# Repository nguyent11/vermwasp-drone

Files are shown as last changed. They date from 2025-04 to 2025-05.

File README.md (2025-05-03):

# Wasp Drone
Senior Capstone Project for CSE 4316 and CSE 4317 Computer System Design Project I and II at UT Arlington Department of Computer Science and Engineering by team Verminator.

## Summary of Work
In this project, we propose a design for an aerial spraying platform. The idea is to have insecticide sprayers mounted onto a drone. Then, the product can be used to spray insecticides on wasp nests, or other insect nests, in hard to reach areas.

This repository contains source code, links to other repositories, STL files for 3D models, and other documentation used in the development of this project.

## Getting Started
This repository contains source code and links to other repositories with source code. After cloning this repository, run the following command to obtain source code from included submodules:
```
  git submodule update --init  --recursive
```

## About the Team
The team is named after Dwayne LaFontant aka The Verminator from Over the Hedge produced by DreamWorks. The team's emblem takes inspiration from Helldivers 2 by Arrowhead Game Studios.

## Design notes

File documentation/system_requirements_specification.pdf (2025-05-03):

## DEPARTMENT OF COMPUTER SCIENCE & ENGINEERING

## THE UNIVERSITY OF TEXAS AT ARLINGTON

## SYSTEM REQUIREMENTS SPECIFICATION

# CSE 4316: SENIOR DESIGN I FALL 2024

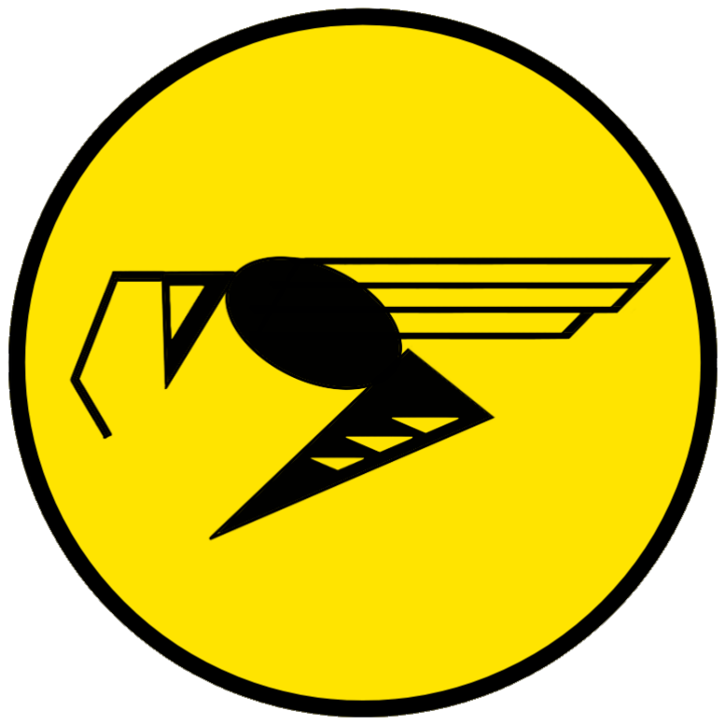
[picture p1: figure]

## VERMINATOR

## WASP DRONE

ISAAC MEDRANO
LUIS NAREZ
TYLER NGUYEN
NISHCHAL SHRESTHA
RAJESH YAKSHO
Verminator - Fall 2024 | page 1 of 28

REVISION HISTORY

Revision | Date | Author(s) | Description
0.1 | 10.01.2024 | TN | document creation
0.2 | 10.12.2024 | IM, LN, TN, NS, RY | complete draft
1.0 | 10.14.2024 | IM, LN, TN, NS, RY | oficial release
2.0 | 05.01.2025 | LN, TN, RY | Updated to reflect changing project requirements

CONTENTS

1 Product Concept | 8
2 Product Description | 9
3 Customer Requirements | 11

4 Packaging Requirements | 15
5 Performance Requirements | 17
6 Safety Requirements | 18

7 Security Requirements | 20
8 Maintenance & Support Requirements | 21
9 Other Requirements | 23
10 Future Items | 24

LIST OF FIGURES

1 | Product Concept of the Wasp Drone | | 9
2 | Wiring Overview (from Cube Orange+ Documentation) | | 21
3 | Power Systems Overview (from Cube Orange+ Documentation) | | 22

### 1 PRODUCT CONCEPT

This section describes the purpose, use and intended user audience for the Wasp Drone product. Wasp Drone is a system that remotely exterminates wasp nests and other pests. Users of Wasp Drone will be able to safely exterminate wasp nests, spray venom, and remotely operate with a controller and live feed camera.

### 1.1 PURPOSE AND USE

Wasp Drone will be sent in to neutralize wasp nests without the need for a human exterminator. The purpose of Wasp Drone is to provide a safe alternative for wasp extermination without putting exterminators in harm’s way. Its venom delivery system can be modified to spray other liquids so there is versatility in agricultural applications (delivering insecticides, herbicides, fertilizer, and water). Wasp Drone’s live feed feature can be used for filming and streaming applications as well.

### 1.2 INTENDED AUDIENCE

- Exterminators: The primary users for this product are wasp exterminators who would benefit from an efficient and safe solution to exterminating wasps and other pests.
- Property Owners: People with an infestation problem on their property(s) looking for an alternative to calling an exterminator.
- Farmers: Agricultural professionals looking to use the sprayer system for other applications on their products.
- Hobbyist: Anyone who intends to take our open-source product and modify it for their drone applications.

### 2 PRODUCT DESCRIPTION

This section provides the reader with an overview of Wasp Drone. The primary operational aspects of the product, from the perspective of end users, maintainers and administrators, are defined here. The key features and functions found in the product, as well as critical user interactions and user interfaces are described in detail.

### 2.1 FEATURES & FUNCTIONS

- Remote Controlled Flight: Controller operates vertical and horizontal drone flight. Programmed with PX4 software.
- Live Feed: Attached drone camera transmits live feed to Wasp Drone app(reach goal). 5.8 GHz radio transmission.
- Sprayer System: Refillable electronic pump keeps container pressurized. Remote-activated sprayer rod dispenses wasp venom.

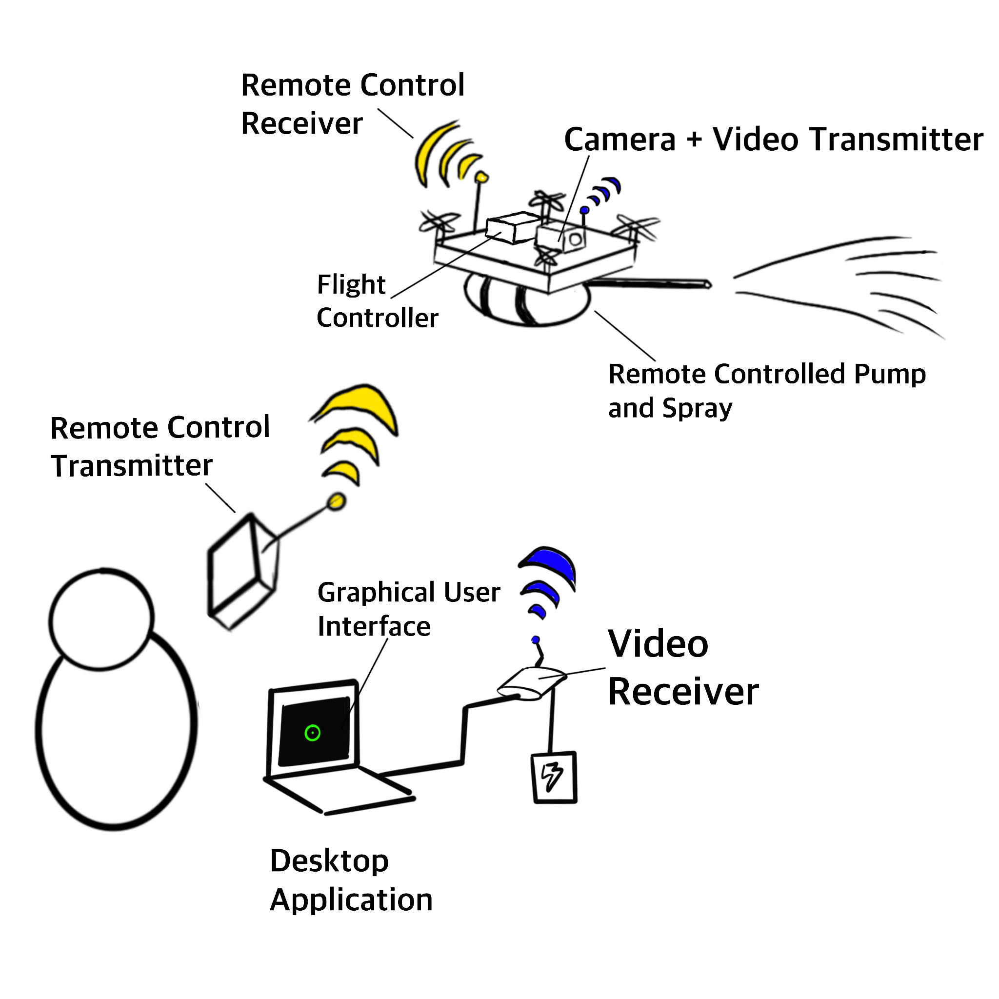
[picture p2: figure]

Figure 1: Product Concept of the Wasp Drone

### 2.2 EXTERNAL INPUTS & OUTPUTS

Data Element | Description | Use
Flight Commands | User data that commands the drone. | Input: Controller input to man the drone. Vertical and horizontal movement. Drone speed.
Phone to Camera Connec-tion(Reach Goal) | Radio connection from the phone to the drone camera | Input: Radio connection from user’s phone to live feed camera.
Sprayer Activation | User data that controls sprayer | Input: Controller input that tog-gles the sprayer.
Live Feed | Camera footage | Output: Camera transmits live footage to the computer

Table 2: Input Output Table

### 2.3 PRODUCT INTERFACES

- Remote Controller: Hardware interface that operates the drone’s flight, landing, and sprayer.
- Wasp Drone App UI(reach goal): A simple UI for the app that connects the user’s phone to the drone

### 3 CUSTOMER REQUIREMENTS

The following requirements detail usability and functional requirements specified by the project’s sponsors, development team, and the intended audience. The customer requirements focus on usability and safety concerns. This is important because the drone will be used to disperse toxic chemicals, so systems must be robust, easy to use, and compliant with safety and environmental regulations.

### 3.1 INTUITIVE USER INTERFACE

### 3.1.1 DESCRIPTION

The drone will make use of standard remote controllers, a FPV camera, and an Android smartphone app(reach goal) to meet this requirement. Industry standard remote controllers will allow the user to pair any controller of their choice with our drone. FPV cameras will allow the user to aim the sprayer and provide vision in hard to reach locations. The drone will have compatible Android app(reach goal) to allow the user to receive live video feeds.

### 3.1.2 SOURCE

Dr. Shawn Gieser and Dr. Chris McMurrough of the Department of Computer Science and Engineering, University of Texas at Arlington.

### 3.1.3 CONSTRAINTS

Controls must account for several factors: 1) the drone must be easy and intuitive to control, 2) the user must be able to have a first-person view of the drone, 3) set up must be doable for inexperienced users within a reasonable amount of time.

### 3.1.4 STANDARDS

Control systems must allow users to use standard controllers on 2.4 GHz signal and communicate with ground station using the MAVLink protocol.

### 3.1.5 PRIORITY

Critical

### 3.2 EFFECTIVE OPERATION IN DAY AND NIGHT CONDITIONS

### 3.2.1 DESCRIPTION

It is typically recommended to remove wasp nests at night due to safety concerns and higher likelihood of encountering all members of the nest. Because of this, the user must be able to pilot the drone during the day and the night. This requirement is fulfilled with a FPV camera with high IR sensitivity. During the day, an additional IR filter can be mounted on the camera to improve daytime image quality. The drone must also meet required safety standards for night time operation including strobe lights and altitude locks.

### 3.2.2 SOURCE

Dr. Shawn Gieser and Dr. Chris McMurrough of the Department of Computer Science and Engineering, University of Texas at Arlington.

### 3.2.3 CONSTRAINTS

Must conform to strict budget.

### 3.2.4 STANDARDS

Federal Aviation Administration (FAA) 14 CFR Part 107: Small Unmanned Aircraft Systems [2]

### 3.2.5 PRIORITY

Moderate

### 3.3 REFILLABLE INSECTICIDE TANK

### 3.3.1 DESCRIPTION

The user must be able to refill the insecticide sprayer in an economical manner using liquid insecticides. A tank will allow for the user to refill using the liquid insecticide of their choice. May apply for exemption due to weight limit.

### 3.3.2 SOURCE

Dr. Shawn Gieser and Dr. Chris McMurrough of the Department of Computer Science and Engineering, University of Texas at Arlington.

### 3.3.3 CONSTRAINTS

Sprayer system packaging must be lightweight to operate drone in a safe manner. The tank must be securely fastened and sealed to protect the user and sensitive electronics.

### 3.3.4 STANDARDS

Federal Aviation Administration (FAA) 14 CFR Part 137: Dispensing Chemicals and Agricultural Products with UAS [1]

### 3.3.5 PRIORITY

High

### 3.4 SAFELY DISPENSE TOXIC CHEMICALS

### 3.4.1 DESCRIPTION

Agricultural drones are typically used to disperse pesticides, herbicides, and fertilizers. Because of this, our drone must comply with federal standards concerning the dispersal of toxic chemicals. Safety for the user and the environment is a major concern. May apply for exemption due to weight limit.

### 3.4.2 SOURCE

Development Team

### 3.4.3 CONSTRAINTS

Electronics will need to be protected. Sprayer system needs to be securely fastened. Sprayer system needs to be lightweight to meet weight limits for FAA regulations and to safely operate the drone.

### 3.4.4 STANDARDS

Federal Aviation Administration (FAA) 14 CFR Part 137: Dispensing Chemicals and Agricultural Products with UAS [1]

### 3.4.5 PRIORITY

Critical

### 3.5 RELIABLE SUBSYSTEMS

### 3.5.1 DESCRIPTION

The drone must be resilient. The mechanics of the drone and the toxic chemical payload poses a risk to the user and the environment. Features such as return to home and landing mode will need to be implemented and enabled in case of emergency situations. Another way to add reliability would be to implement redundant systems.

### 3.5.2 SOURCE

Development Team

### 3.5.3 CONSTRAINTS

Need to balance cost with redundancy and reliability. The team does not have the budget to build a fully redundant system, so failsafes need to be implemented instead.

### 3.5.4 STANDARDS

None

### 3.5.5 PRIORITY

Critical

### 3.6 GEOFENCING(REACH GOALS)

### 3.6.1 DESCRIPTION

The FAA has strict safety definitions concerning airspace that drones and other unmanned aircraft systems (UAS) must abide by. For the safety of the user and external parties, geofencing systems will be implemented and interact with the onboard GPS module to enforce a strict airspace.

### 3.6.2 SOURCE

Development Team

### 3.6.3 CONSTRAINTS

The PX4 firmware needs to be modified to enforce stricter limits on the user to adhere to FAA regulation. Accuracy of the geofencing system is bounded by the capabilities of the drone’s GPS module. The testing site must have allowable airspace to test this subsystem.

### 3.6.4 STANDARDS

Federal Aviation Administration (FAA) 14 CFR Part 107: Small Unmanned Aircraft Systems [2]

### 3.6.5 PRIORITY

Moderate

### 3.7 THERMAL IMAGING CAMERA

### 3.7.1 DESCRIPTION

Many wasps hide nests in hard to reach or hard to find locations, posing a hazard to unaware victims. Thermal imaging cameras are an optional solution to allow the user to locate hidden nests.

### 3.7.2 SOURCE

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

### 3.7.3 CONSTRAINTS

Common thermal imaging cameras, such as those by FLIR, are prohibitively expensive. Existing FAA regulations need to be met and local laws regarding filimg, photographing, or observing people or objects from unmanned aircraft may prohibit testing of such a system.

### 3.7.4 STANDARDS

Federal Aviation Administration (FAA) 14 CFR Part 107: Small Unmanned Aircraft Systems [2]

### 3.7.5 PRIORITY

Low

### 4 PACKAGING REQUIREMENTS

This project is designed to be modular and work with an entire ecosystem of parts and components. For example, the customer will have the option of purchasing a complete drone and sprayer, or be able to use the sprayer on a drone of their choice. To do so, our team will develop with industry standards in mind and keep our project open source.

### 4.1 FREE AND OPEN SOURCE SOFTWARE

### 4.1.1 DESCRIPTION

To facilitate future use of the drone project, source code and documentation will be made available for the open source community, drone enthusiasts, and will be licensed in a way to allow for commercial use cases.

### 4.1.2 SOURCE

Dr. Shawn Gieser and Dr. Chris McMurrough of the Department of Computer Science and Engineering, University of Texas at Arlington, and the Development Team

### 4.1.3 CONSTRAINTS

Software licensing must be permissive, allowing a wide range of use cases. Source code will need to be easy to follow and easy to use. Build guides will be provided for the user and similar hardware will be specified as known compatible options for the customer.

### 4.1.4 STANDARDS

The PX4 Autopilot firmware is licensed under the 3-clause BSD license. It is a permissive license that allows for hobbyist and commercial use. Our additional modules will be licensed under the MIT License. The MIT License is also permissive and will allow for many use cases.

### 4.1.5 PRIORITY

Critical

### 4.2 PX4 AUTOPILOT COMPATIBLE

### 4.2.1 DESCRIPTION

PX4 Autopilot is an open source firmware package with autopilot and remote controlled capabilities. Building for the PX4 Autopilot system allows users who want to bring their own equipment to utilize our software. Additionally, our software can be added onto existing PX4 projects to provide more functionality.

### 4.2.2 SOURCE

Development Team

### 4.2.3 CONSTRAINTS

For budgeting reasons, we cannot test our firmware with all compatible flight controllers on the PX4 ecosystem. To ensure that our software is compatible, we need to follow strict adherence to the existing PX4 documentation and programming model.

### 4.2.4 STANDARDS

PX4 Autopilot Documentation [3]

### 4.2.5 PRIORITY

Critical

### 4.3 SOFTWARE DISTRIBUTION

### 4.3.1 DESCRIPTION

Our project will be both a product that can be purchased off the shelf, and as a firmware package that experienced developers and enthusiasts can integrate into their projects.

### 4.3.2 SOURCE

Dr. Shawn Gieser and Dr. Chris McMurrough of the Department of Computer Science and Engineering, University of Texas at Arlington, and the Development Team

### 4.3.3 CONSTRAINTS

A public code repository is necessary to enable developers and enthusiasts to use our software. Software delivered to customers would be included in the purchase of a drone. In this case, software will be flashed on the controller prior to sale.

### 4.3.4 STANDARDS

MIT License

### 4.3.5 PRIORITY

High

### 5 PERFORMANCE REQUIREMENTS

The wasp-killing drone is a product designed for a quick and efficient elimination of wasps in various environments. Performance is critical to ensure the drone can perform tasks with no delay, ensuring a quick response to wasp threats. The drone must operate within a specified time limits for key functions, including system initialization, takeoff, navigation,wasp detection and extermination. Operational efficiency is required to maintain a high level of effectiveness.

### 5.1 WASP DETECTION AND ELIMINATION TIME

### 5.1.1 DESCRIPTION

The user must be able to identify a wasp using the FPV camera(reach goal). There needs to be a low latency connection between the drone and the base station to facilitate a quick elimination time. The drone must stay in the air long enough to saturate the wasp nest with insecticide.

### 5.1.2 SOURCE

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

### 5.1.3 CONSTRAINTS

The cost of the camera used to identify the nest and the overall cost of the drone and battery packs must be kept at a minimum due to the low budget.

### 5.1.4 STANDARDS

IEEE 1233: system requirement specification
ISO 9126 - 1: Software Engineering - Product Quality UL 3030: Unmanned Aerial Vehicles Safety Standards

### 5.1.5 PRIORITY

High: The primary function and purpose is to eliminate wasps quickly and effectively.

### 6 SAFETY REQUIREMENTS

The wasp-killing drone is designed to operate safely in residential and outdoor environments which ensures that is functionality does not harm users or nearby animals. The safety requirements ensure that the drone operates with established guidelines to prevent minimal injuries or exposure to harmful substances. The drone design will minimize risks by avoiding sharp components, restricting the use of hazardous materials and ensuring anything with electrical elements are shielded.

### 6.1 PROPELLER SAFETY SHIELDING

### 6.1.1 DESCRIPTION

All drone propellers will protected with safety shields(reach goal) to prevent accidental contact with users, pets or bystanders.

### 6.1.2 SOURCE

CSE Senior Design laboratory policy

### 6.1.3 CONSTRAINTS

The propeller safety shields(reach goal) must not interfere with the drones flight capability. The shield must be lightweight yet durable.

### 6.1.4 STANDARDS

ASTM F2908: standard specification for consumer unmanned aircraft systems (UAS) ISO 12100: Safety of Machinery - General Principles for Design

### 6.1.5 PRIORITY

High

### 6.2 NON-TOXIC MATERIALS

### 6.2.1 DESCRIPTION

All materials used in the drone construction must be non-toxic and safe for human and animal exposure. The system must not release any harmful chemicals during operation.

### 6.2.2 SOURCE

CSE Senior Design laboratory policy

### 6.2.3 CONSTRAINTS

Materials used in the extermination system must be effective in killing wasps but must not pose a risk to people.
The use of toxins are prohibited, which limits the types of chemicals used

### 6.2.4 STANDARDS

RoHS Directive 2011/65/EU on the restriction of hazardous substances
ISO 10993-5: Biological Evaluation of Medical Devices

### 6.2.5 PRIORITY

High

### 6.3 ELECTRICAL INSULATION

### 6.3.1 DESCRIPTION

All electrical components within the drone must be properly insulated to prevent shocks(reach goals). Wires should be secured and shielded to avoid exposure during operation.

### 6.3.2 SOURCE

CSE Senior Design laboratory policy

### 6.3.3 CONSTRAINTS

All wiring must adhere to insulation standards and be tested for durability during drone operation.

### 6.3.4 STANDARDS

NFPA 70: National Electric Code (NEC)
IEC 60364: Low-voltage electrical installations

### 6.3.5 PRIORITY

High

### 7 SECURITY REQUIREMENTS

The security requirement for the wasp drone project is to ensure secure operation of the drone and its components, the camera and the spray mechanism, without interference from any external sources.

### 7.1 WIRELESS COMMUNICATION SECURITY(REACH GOAL)

### 7.1.1 DESCRIPTION

The drone will wirelessly communicate with a smartphone for camera feed and spray control. Although no data will be stored, securing communication between the drone and the smartphone is important to prevent unauthorized control. The live camera feed between the drone and the smartphone must be secured to prevent any privacy concerns and misuse of the video stream by any third party. The wireless control mechanism for operating the spray system also requires security to ensure safe and authorized communication.

### 7.1.2 SOURCE

Team decision based on the system design.

### 7.1.3 CONSTRAINTS

The wireless communication must operate within the drone’s flight range. Security measures, such as encrypted communication (e.g., WPA2 or equivalent), can be considered to avoid unauthorized access or interference by external agents.

### 7.1.4 STANDARDS

None specified at this stage.

### 7.1.5 PRIORITY

High

### 8 MAINTENANCE & SUPPORT REQUIREMENTS

The requirements for maintaining and supporting the drone during the testing stage and the operating stage are as follows.

### 8.1 DRONE MAINTENANCE AND TROUBLESHOOTING

### 8.1.1 DESCRIPTION

We have chosen a quadcopter design for the drone. As we add and integrate more components to our drone, maintaining the drone will become increasingly challenging and costly. Routine maintenance will involve swapping and recharging batteries as the batteries run out quickly when operating the drone. To ensure continuous operation, ideally, multiple batteries will be available for quick swaps. Additional maintenance will include replacing components that might get damaged during the testing phase and ensuring both hardware and software are functioning correctly. Troubleshooting can be guided by the schematics and flight controller documentation, and any system modifications can be made by referencing the schematic diagrams for necessary adjustments.

### 8.1.2 SOURCE

The Orange Cube+ quick start guide.

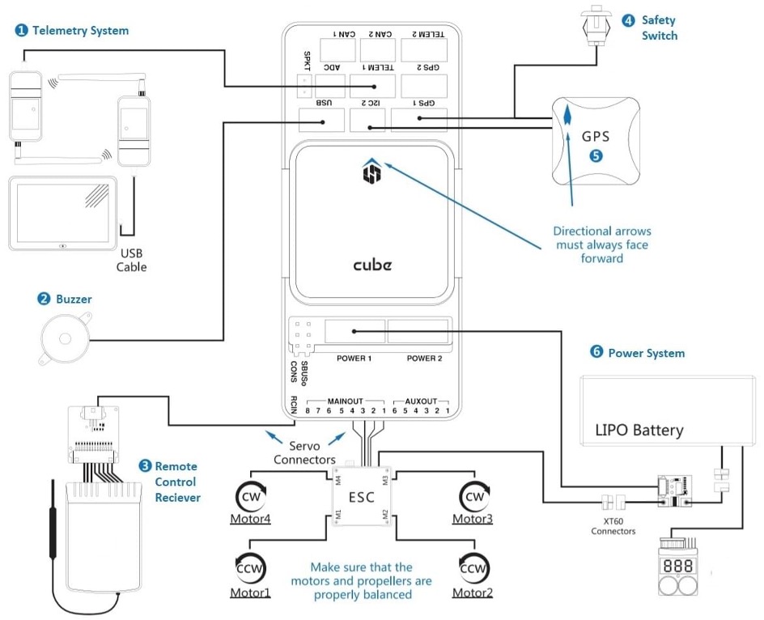
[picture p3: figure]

Figure 2: Wiring Overview (from Cube Orange+ Documentation)

### 8.1.3 CONSTRAINTS

Complexity of the flight control system might become an issue among team members. Identifying errors and failures might also become challenging because of the team not having prior experience with

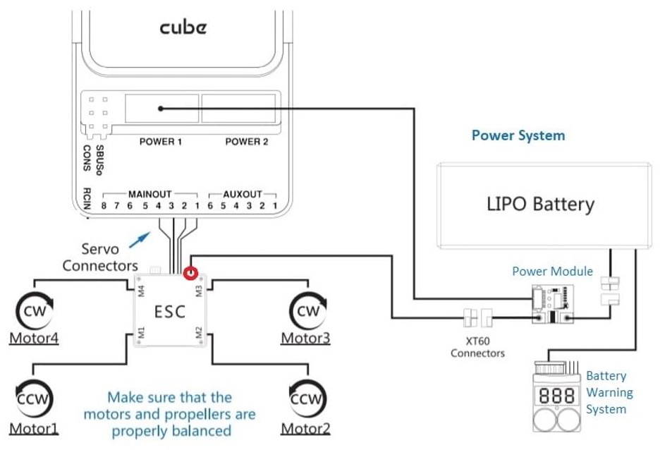
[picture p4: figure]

Figure 3: Power Systems Overview (from Cube Orange+ Documentation)

drones. Components like propellers, batteries, and the spray mechanism will require regular checks and potential replacements during the testing phase, which may lead to delays in operation and added shipping times for the replacements. Battery charging and swapping times will also impact the drone’s operational availability. Additionally, budget constraints may arise due to the need for extra parts caused by possible failures during testing.

### 8.1.4 STANDARDS

PX4 software guidelines and Cube Wiring quick start.

### 8.1.5 PRIORITY

High

### 9 OTHER REQUIREMENTS

### 9.1 WASP KILLING DRONE CUSTOMIZATION

### 9.1.1 DESCRIPTION

The Wasp Killing Drone project will be designed with future enhancements and customization capabilities to support various applications in targeting and eliminating wasp nests. This includes ensuring compatibility with additional expansion decks, sensors, and pesticide delivery systems to adapt to evolving project requirements. The team will also implement a video streaming system that provides real-time visual feedback for enhanced situational awareness during operations. These customization features will be integrated into the project’s architecture during the development phase, allowing for new functionalities to be designed and tested.

### 9.1.2 SOURCE

Project Sponsors: Dr. Gieser and Dr. McMurrough

### 9.1.3 CONSTRAINTS

Customization may encounter constraints related to hardware limitations, compatibility issues with new components, and the need to maintain overall system stability. Thorough testing will be required to ensure that new additions do not adversely affect the drone’s performance or safety. Given the delicate nature of the hardware, minimal intervention during handling and assembly is crucial to prevent damage.

### 9.1.4 STANDARDS

No specific standards apply for this requirement.

### 9.1.5 PRIORITY

Low

### 10 FUTURE ITEMS

### 10.1 DRONE ASSEMBLY

### 10.1.1 DESCRIPTION

The drone assembly process will involve carefully assembling all ordered components, ensuring that they fit together properly and function as intended. This stage will include thorough checks for compatibility and safety before proceeding to the testing phase.

### 10.1.2 SOURCE

Development Team

### 10.1.3 CONSTRAINTS

Assembly must adhere to manufacturer specifications and safety guidelines to avoid damage to delicate components.

### 10.1.4 STANDARDS

ASTM F2910-14: Standard Guide for the Evaluation of the Safety of Small Unmanned Aircraft Systems

### 10.1.5 PRIORITY

Critical

### 10.2 MANUAL CONTROL

### 10.2.1 DESCRIPTION

The drone shall be controlled manually using a controller which allows operators to navigate freely and respond dynamically to obstacles.

### 10.2.2 SOURCE

Sponsors

### 10.2.3 CONSTRAINTS

Operators must maintain awareness of environmental conditions and obstacles while controlling drone manually.

### 10.2.4 STANDARDS

No specific standards apply to this requirement.

### 10.2.5 PRIORITY

Critical

### 10.3 CAMERA AND VIDEO STREAMING

### 10.3.1 DESCRIPTION

The Wasp Killing Drone will be equipped with a camera and a video streaming application to facilitate real-time obstacle detection and navigation during operations.

### 10.3.2 SOURCE

Sponsors

### 10.3.3 CONSTRAINTS

The video streaming system must operate effectively under varying environmental conditions and maintain a stable connection for real-time feedback.

### 10.3.4 STANDARDS

No specific standards apply to this requirement.

### 10.3.5 PRIORITY

Critical

### 10.4 PESTICIDE APPLICATION SYSTEM

### 10.4.1 DESCRIPTION

The drone shall integrate a pesticide application system to deliver pesticides precisely to targeted wasp nests without affecting surrounding environments.

### 10.4.2 SOURCE

Sponsors

### 10.4.3 CONSTRAINTS

The pesticide system must comply with safety regulations regarding pesticide use and ensure environmental protection measures are in place.

### 10.4.4 STANDARDS

EPA regulations on pesticide application.

### 10.4.5 PRIORITY

Critical

### 10.5 DOCUMENTATION

### 10.5.1 DESCRIPTION

Comprehensive documentation, including user manuals, pesticide application guidelines, setup guides, and troubleshooting instructions(some reach goals), will be provided in both digital and printed formats for ease of access.

### 10.5.2 SOURCE

Sponsors

### 10.5.3 CONSTRAINTS

Documentation must be clear, concise, and easily understandable, accommodating users with varying technical expertise.

### 10.5.4 STANDARDS

None

### 10.5.5 PRIORITY

Critical

### 10.6 COMMUNICATION RELIABILITY

### 10.6.1 DESCRIPTION

Communication reliability refers to the dependability of the communication system between the Wasp Killing Drones and the central control system (ROS). A highly reliable communication system ensures seamless data exchange and coordination within the drone swarm, which is essential for maintaining situational awareness and executing maneuvers without interruptions or data loss during pest control operations.

### 10.6.2 SOURCE

Development Team

### 10.6.3 CONSTRAINTS

Limitations imposed by communication protocols, signal interference, or environmental factors affecting wireless communication performance.

### 10.6.4 STANDARDS

MAVLink Protocol. FCC defined 2.4 GHz and 5.8 GHz bands

### 10.6.5 PRIORITY

Critical

### 10.7 OPERATION SPEED

### 10.7.1 DESCRIPTION

Operation speed refers to the ability of the Wasp Killing Drone to execute commands and respond to inputs rapidly and efficiently. This capability is crucial for tasks such as trajectory planning and communication between drones, allowing it to operate swiftly. In dynamic environments, such as pest control missions, operational speed enables the drones to adapt to new information and maintain situational awareness in real-time, enhancing their effectiveness in locating and targeting wasp nests.

### 10.7.2 SOURCE

Development Team

### 10.7.3 CONSTRAINTS

Limitations imposed by hardware capabilities, communication bandwidth, and environmental factors affecting drone performance.

### 10.7.4 STANDARDS

Industry benchmarks for response times in a controlled environment.

### 10.7.5 PRIORITY

Critical

### 10.8 FAULT TOLERANCE(REACH GOALS)

### 10.8.1 DESCRIPTION

Fault tolerance refers to the Wasp Killing Drone swarm system’s capability to withstand and mitigate the impact of individual drone failures or malfunctions. Robust fault tolerance capabilities are essential to minimize the impact failures and ensure continued operation and mission effectiveness. In the event of catastrophic failures, failsafes must be implemented to reduce environmental harm, bodily injury, and loss of the drone.

### 10.8.2 SOURCE

Development Team

### 10.8.3 CONSTRAINTS

Limitations imposed by hardware and communication protocols for fault detection and recovery. Low budget limits how much redundancies can be implemented.

### 10.8.4 STANDARDS

FAA 14 CFR Part 107

### 10.8.5 PRIORITY

Critical

REFERENCES

[1] Department of Transportation Federal Aviation Administration. 14 CFR Part 137, 1965 ammended 2018.
[2] Department of Transportation Federal Aviation Administration. 14 CFR Part 107, 2016.
[3] PX4. PX4 Guide (Main), updated 2024.

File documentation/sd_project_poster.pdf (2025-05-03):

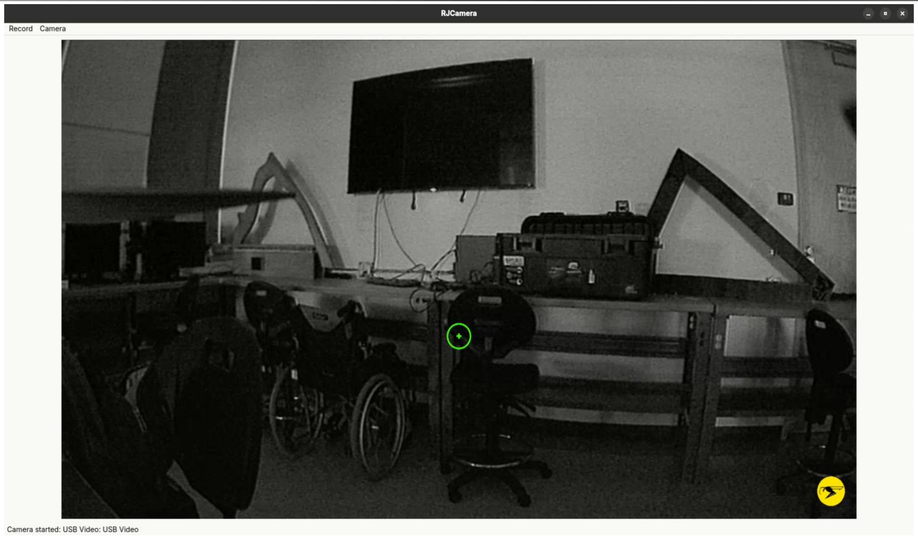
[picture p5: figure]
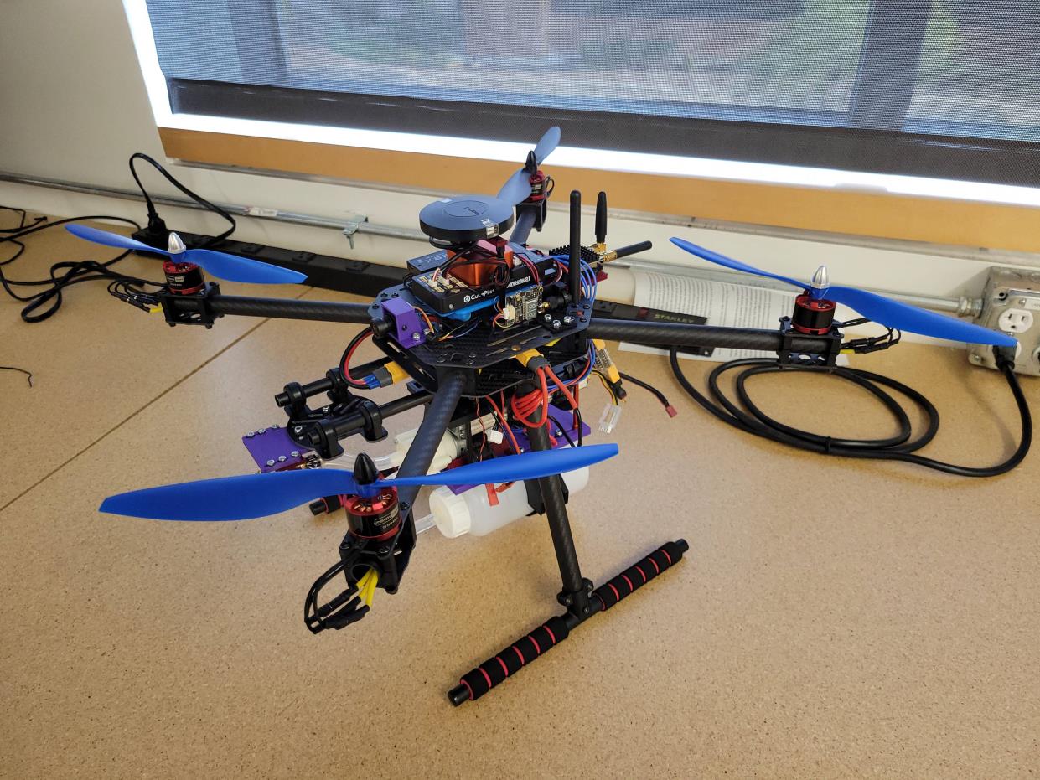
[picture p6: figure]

d

Nguyen, T., Medrano, I., Narez, L., Yaksho, R., Shrestha, N.

# Verminator Wasp Drone

Wasps and other insects pose a risk to people, especially small children. This project is designed to bring aerial spray drones from the agricultural industry to hobbyists,
homeowners, and small business owners.

This drone will allow the user to spray insects from a safe distance or apply insecticides
to hard-to-reach areas.

Key requirements:
- Camera system allowing for easy to maneuver in tight spaces without line of sight.
- Sprayer needs to have enough range and pressure to spray insect nests from a safe distance.
- Drone should be modular to allow for various payloads and missions.
- Drone design and implementation must be free and open source

### Conclusions and Future Work

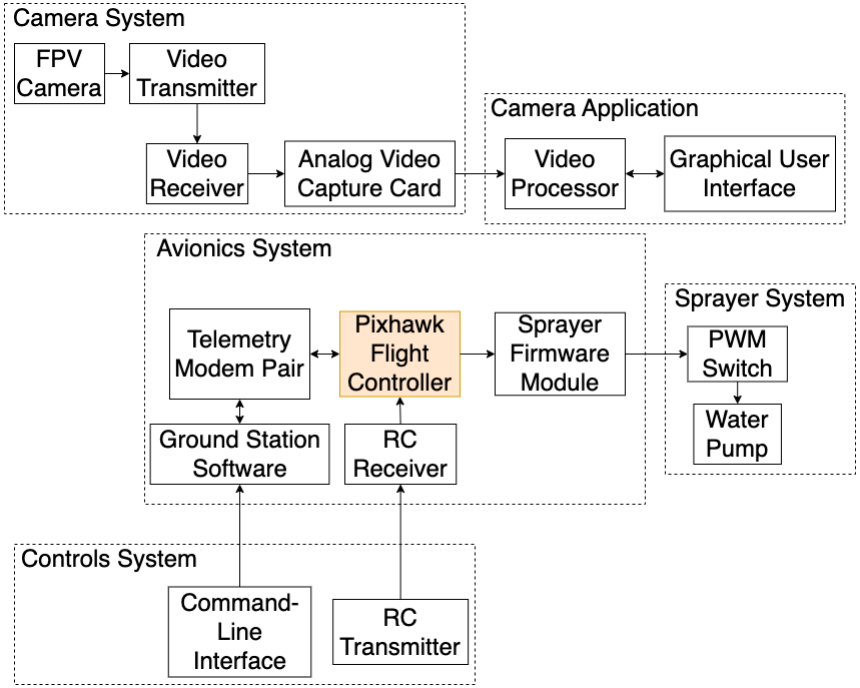
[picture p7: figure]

1. PX4 Development Team. PX4 Autopilot. (2025). Accessed: Dec. 20, 2024. [Online]. Available: https://github.com/PX4/PX4-Autopilot
2. DJI Agriculture. Agricultural Drone Industry Insight Report. (2023). DJI. Available: https://www1.djicdn.com/cms_uploads/ckeditor/attachments/9171/03e81f9a23cf4df447b66 c91c43d929a.pdf
3. S. Spoorthi, B. Shadakshrarappa, S. Suraj, V. K. Manasa. "Freyr drone: Pesticide/fertilizers spraying drone - an agricultural approach". 2017 2nd International Conference on Computing and Communications Technologies (ICCCT). 2017, pp. 252-255, doi: 10.1109/ICCCT2.2017.7972289.

### QR Code To Website or Paper Goes Here

### References

### Implementation Details and Test Plan

Background | Architectural Design

### Key Requirements

## Hardware

Drone
- CubePilot Cube Orange+ flight controller with PX4 firmware
- 500mm carbon fiber airframe
- 2212 920KV motors with 10" propellers
- 4-in-1 40A electronic speed controller

The Verminator Wasp Drone is a remotecontrolled aerial spraying platform modelled after larger and more expensive agricultural drones. The drone is outfitted for the removal of wasp nests and is equipped with a first-person camera and an insecticide sprayer to neutralize wasp nests from a safe distance. Users can remotely pilot the drone with the first-person camera and industry-standard RC receiver. Custom firmware modules to control the sprayer allows for programmatic control and automation for future applications. The Verminator Wasp Drone proposes a new application of agricultural drones, but without the burdensome costs that stem from commercial operations.

April 2025

## Senior Design

Camera System
- RunCam Night Eagle 3 v2 low-light sensitive camera
- 5.8 GHz analog video transmitter and receiver
- Analog-to-digital video capture card

Sprayer System
- 12V 0.3A DC Water pump
- 12V 20A DC PWM controlled switch

## Software

Desktop Camera Application
- Qt6 Multimedia for camera capture
- Qt6 for graphical user interface
- OpenCV C++ for alpha compositing frames and overlay images

## Test Plan

Hardware
- Validated flight controller firmware modifications in controlled environments using test-driven development.

Software
- Tested using a variety of USB video devices for interoperability.
- Tested on a variety of Debian-based and RHEL-based Linux distributions.

Conclusion
We successfully created a prototype that demonstrates the feasibility of an affordable aerial spraying platform and meets the requirements of our sponsor.
Future Work
- Switch to larger 650mm airframe and 6S power system for higher payload.
- Outfit the drone with different payloads to become a modular multi-role system. Acknowledgements
We would like to thank our sponsor and instructor, Dr. Shawn Gieser, and our lab coordinator, Steve McDermott, for their assistance on this project.

Figure 1. Architectural design diagram

### Camera System

Provides a live camera stream for the camera application. Frames are sent through 5.8 GHz radio and are received by an analog video capture card.

### Camera Application

Processes frames from the analog video capture card using OpenCV. Displays frames to the user with Qt6.

### Controls System

Provides user input for the flight controller. Drone's functions can be controlled programmatically through the command line or radio control.

### Avionics System

Serves as the brain of the drone and is centered around a flight controller with the PX4 firmware. The flight controller receives inputs from the user or automated commands through a RC receiver or telemetry radios. Those commands are used to execute functions on the flight controller.

### Sprayer System

The sprayer is toggled through a PWMcontrolled switch. The PWM signal is sent by the flight controller in response to RC inputs, or programmatically through a custom module that was added to the PX4 firmware.

Figure 2. Completed build of drone.

Figure 3. Camera application with feed in a very low-light environment.

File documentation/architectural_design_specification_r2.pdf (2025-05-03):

## DEPARTMENT OF COMPUTER SCIENCE & ENGINEERING

## THE UNIVERSITY OF TEXAS AT ARLINGTON

## ARCHITECTURAL DESIGN SPECIFICATION

# CSE 4316: SENIOR DESIGN I FALL 2024

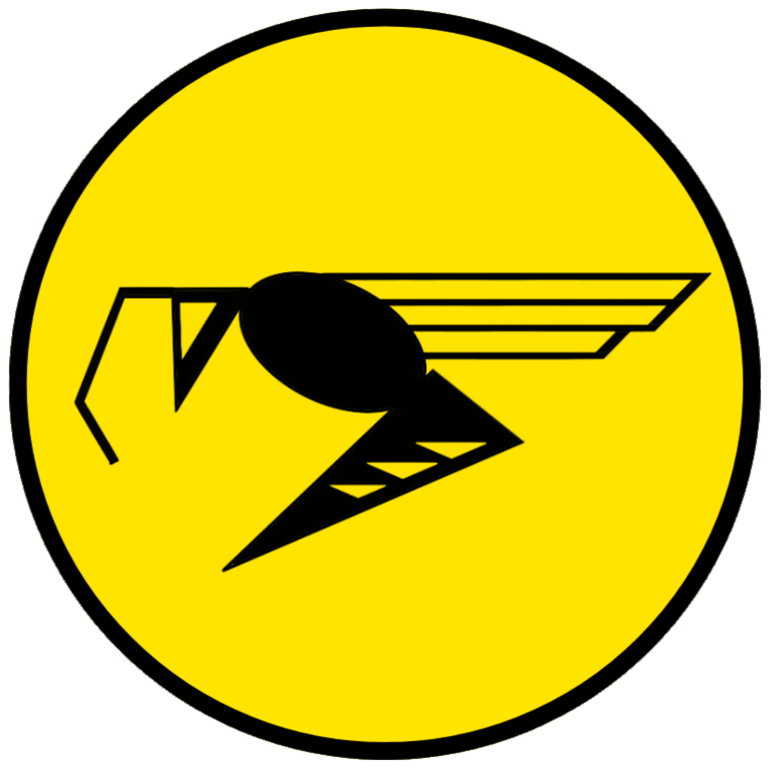
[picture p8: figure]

## VERMINATOR

## WASP DRONE

ISAAC MEDRANO
LUIS NAREZ
TYLER NGUYEN
NISHCHAL SHRESTHA
RAJESH YAKSHO
Verminator - Fall 2024 | page 1 of 27

REVISION HISTORY

Revision | Date | Author(s) | Description
0.1 | 10.31.2024 | TN | document creation
0.2 | 11.02.2024 | TN, IM, RY, LN, NS | complete draft
1.0 | 11.04.2024 | TN, IM, LN, RY, NS | official release
2.0 | 04.30.2025 | TN, RY | Updated design with better reflection of final hard-ware.

CONTENTS

1 Introduction | 5
2 System Overview | 6
3 Subsystem Definitions & Data Flow | 8
4 Avionics System | 9
5 Power and Propulsion System | 14
6 Controls System | 17
7 Camera Application System | 19
8 Sprayer System | 22
9 Camera System | 24

LIST OF FIGURES

1 | A simple architectural layer diagram | | 6
2 | Full architectural design diagram showing data and power for the drone | | 8
3 | Avionics system highlighting flight controller | | 9
4 | Avionics system highlighting telemetry subsystem | | 10
5 | Avionics system highlighting GPS Module | | 11
6 | Avionics system highlighting sprayer modules | | 12
7 | Propulsion system highlighting motors and ESC | | 14
8 | Propulsion system highlighting power subsystem | | 15
9 | Controls system highlighting RC subsystem | | 17
10 | Controls system highlighting Shell subsystem | | 18
11 | Camera application system highlighting the video processor subsystem | | 19
12 | User interface system highlighting information overlay | | 20
13 | Sprayer system highlighting PWM-controlled switch and pump | | 22
14 | Camera system highlighting FPV camera | | 24
15 | Camera system highlighting video transmitter | | 25
16 | Camera system highlighting video transmitter | | 25

LIST OF TABLES

2 | Subsystem interfaces | | 10
3 | Subsystem interfaces | | 11
4 | Subsystem interfaces | | 12
5 | Subsystem interfaces | | 13
6 | Subsystem interfaces | | 15
7 | Subsystem interfaces | | 16
8 | Subsystem interfaces | | 17
9 | Subsystem interfaces | | 18
10 | Subsystem interfaces | | 20
11 | Subsystem interfaces | | 21
12 | Subsystem interfaces | | 23
13 | Subsystem interfaces | | 24
14 | Subsystem interfaces | | 25
15 | Subsystem interfaces | | 26

### 1 INTRODUCTION

The Wasp Drone is a remote-controlled device designed for safe and efficient wasp extermination, using a live-feed camera and an insecticide delivery system to neutralize wasp nests from a distance. The drone’s spray system can be used for agricultural tasks like applying insecticides, herbicides, fertilizers, or water, making it a versatile tool for various applications. Key requirements include real-time video streaming, precise navigation, and customizable spray options, ensuring effective operation in diverse environments. The primary users include professional exterminators, property owners seeking an alternative to traditional pest control, farmers who can utilize its spraying capabilities, and hobbyists interested in modifying this open-source product for unique drone applications [1].

### 2 SYSTEM OVERVIEW

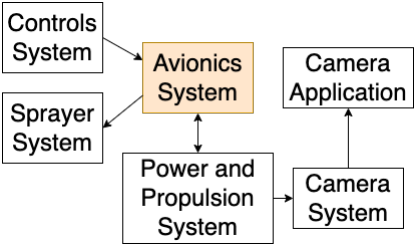
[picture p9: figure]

Figure 1: A simple architectural layer diagram

### 2.1 AVIONICS SYSTEM LAYER DESCRIPTION

The avionics system layer serves as the brain of the drone and contains the flight controller. User commands are fed into the flight controller through transmissions from the ground station or from a remote controller. Commands are passed to each individual component by the avionics system to perform an action. The avionics layer is composed of a flight controller (Cube Orange+ in this case), a telemetry subsystem (containing a telemetry radio, ground station, and related software for telemetry components), the GPS Module, and the Sprayer Firmware Module. The flight controller is used to control inherent drone functions and payload functions to carry out the drone’s mission. The telemetry subsystem is needed to report flight data to the user and ground station. A GPS module is required for flight and is used to report location data to ground station.The sprayer firmware module controls and automates the operation of the drone’s sprayer system.

### 2.2 POWER AND PROPULSION SYSTEM LAYER DESCRIPTION

The power and propulsion system layer ensures that the drone can safely and effectively operate its motors and provides power for other systems in the drone. This layer is mainly composed of motors, electronic speed controllers (ESCs), and a Lithium-ion polymer (LiPo) battery. The motors and ESCs in this layer are used to provide the thrust necessary to lift the drone and the mission payload.

### 2.3 CONTROLS SYSTEM LAYER DESCRIPTION

The Controls System Layer serves as the primary interface for operator input, managing both the drone’s flight and commands for attached payloads. It encompasses two distinct control methods: the Shell

Subsystem, which enables programmatic operation through a ground station command-line interface, and the RC Subsystem, facilitating direct, real-time manual control via a remote transmitter.

### 2.4 CAMERA APPLICATION LAYER DESCRIPTION

The Camera Application layer provides visual feedback for the user. Through a desktop application, the user can view a live feed from the camera in order to help piloting outside line-of-sight.

### 2.5 SPRAYER SYSTEM LAYER DESCRIPTION

The Sprayer Layer’s operation centers on a liquid pump activated via a PWM-controlled switch. This mechanism connects to the flight controller’s auxiliary outputs, highlighting the Verminator Wasp Drone’s modular design for controlling various payload devices.

### 2.6 CAMERA SYSTEM LAYER DESCRIPTION

The Camera System Layer in the wasp-killing drone is designed to provide real-time visual monitoring and transmission capabilities, essential for target identification. This layer consists of three subsystems: the FPV Camera Subsystem, the Video Transmission Subsystem, and the Video Capture Subsystem. The FPV Camera Subsystem uses a very low-light capable camera to capture wide angle frames of the view from the drone. The Video Transmission Subsystem is used to send video frames from the camera to the host device using analog radio. The Video Capture Subsystem presents the analog video as a USB video device for the host to process.

### 3 SUBSYSTEM DEFINITIONS & DATA FLOW

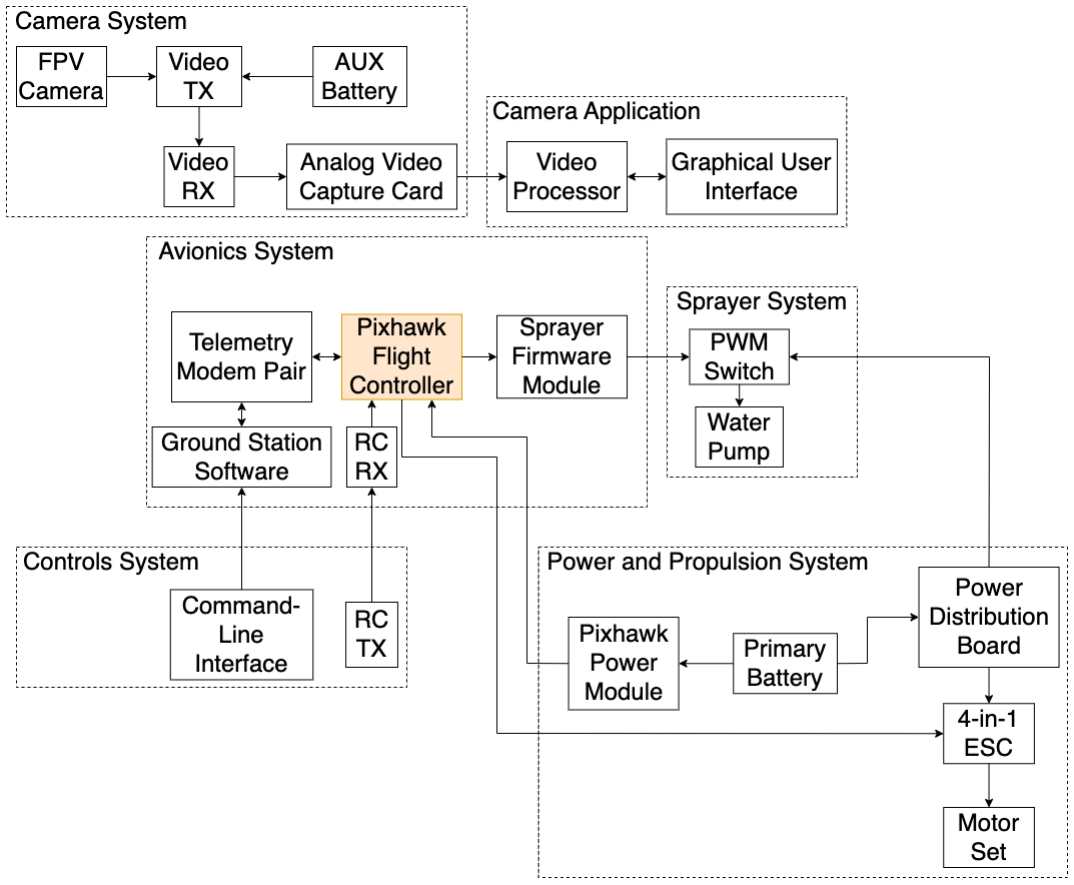
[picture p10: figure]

Figure 2: Full architectural design diagram showing data and power for the drone.

### 4 AVIONICS SYSTEM

The avionics system serves as the "brain" of the drone. Commands issued by the user to activate various equipment and control the drone must first pass through the avionics system. The avionics layer is composed of the flight controller, the telemetry subsystem, the GPS module, and the sprayer firmware module.

### 4.1 FLIGHT CONTROLLER SUBSYSTEM

The flight controller functions as the central processing unit of the avionics system. It receives input from the user and various sensors, processes the data through its firmware, and then generates appropriate actions for the drone. As such, the flight controller and its firmware directly control all components of the drone.

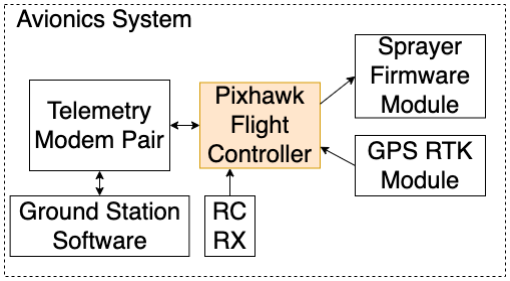
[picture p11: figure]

Figure 3: Avionics system highlighting flight controller

### 4.1.1 ASSUMPTIONS

It is assumed that all sensors, peripherals, and connected subsystems (like the telemetry components, GPS, RC receiver, ESCs, power module, and sprayer module) are fully compatible with the Cube Orange+ flight controller and PX4 firmware.

### 4.1.2 RESPONSIBILITIES

The flight controller subsystem is responsible for processing data from all connected sensors to determine drone’s real-time state. Based on this sensor fusion and internal programming, it executes complex flight control algorithms necessary to stabilize the drone and enable it to follow desired flight paths. It sends the appropriate control signals to the motor controllers and other actuators to achieve desired movements.
Furthermore, it serves as the primary interface for receiving and interpreting manual pilot commands from the RC receiver, exchanging telemetry data and accepting new commands from the ground station via the telemetry subsystem, and providing control interfaces for integrated payload systems, such as the sprayer firmware module.

### 4.1.3 SUBSYSTEM INTERFACES

Table 2: Subsystem interfaces

ID | Description | Inputs | Outputs
#01 | MAVLink protocol wireless interface to Telemetry Modem Pair | Data from Teleme-try Modem Pair | Data to Telemetry Modem Pair

#02 | Wireless RC Link (SBUS, PPM, CRSF) to RC receiver | RC Commands | None

#03 | uORB topic publishing to sprayer firmware module | None | Actuator com-mands

#04 | DroneCAN protocal wired interface to GPS RTK Module | Positional Data | None

### 4.2 TELEMETRY SUBSYSTEM

The telemetry subsystem enables the drone to communicate with the ground station. It works by receiving commands from the ground station and transmitting telemetry data back to it. Telemetry software is built into the flight controller, so only additional hardware is needed to facilitate a radio connection. In this case, antennas are connected to both the telemetry radio and the receiving ground station. Off-the-shelf software manages the implementation.

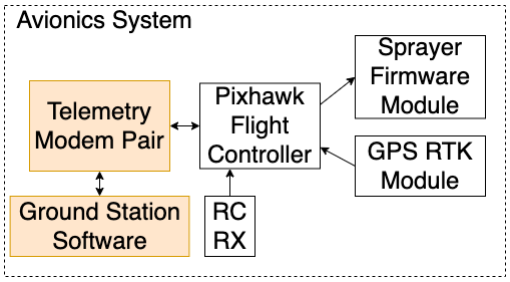
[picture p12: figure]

Figure 4: Avionics system highlighting telemetry subsystem

### 4.2.1 ASSUMPTIONS

It is assumed that the telemetry components are fully compatible with the Cube Orange+ flight controller and operate using the MAVLink protocol.

### 4.2.2 RESPONSIBILITIES

The telemetry subsystem is made up of a computer running ground station software, telemetry reporting firmware on the flight controller, and antennas for each component to transmit and receive data.
The ground station is used to issue commands to the drone and receive telemetry data from the drone’s flight controller.

Each antenna on the ground station and the telemetry radio is used to establish a connection between the telemetry system and the ground station.

### 4.2.3 SUBSYSTEM INTERFACES

Table 3: Subsystem interfaces

ID | Description | Inputs | Outputs
#01 | MAVLink protocol 900 MHz wireless signal between telemetry radio and ground station | Commands | Telemetry Data

### 4.3 GPS SUBSYSTEM

The GPS subsystem determines the position of a drone and plays a critical role in navigation.

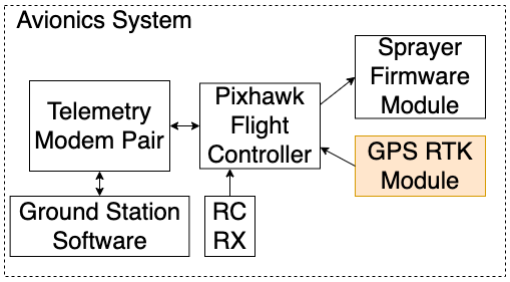
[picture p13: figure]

Figure 5: Avionics system highlighting GPS Module

### 4.3.1 ASSUMPTIONS

The selected GPS module is assumed to be compatible with PX4 Autopilot systems and uses the DroneCAN protocol for communication.

### 4.3.2 RESPONSIBILITIES

The GPS module is responsible for reporting data to the flight controller to aid in positioning and navigation. The chosen GPS module is a RTK DroneCAN GPS allowing for centimeter-level accuracy.
The GPS module is a plug-and-play subsystem that interacts with PX4 and Ardupilot systems outof-the-box. It will only transmit navigational data to the flight controller.

### 4.3.3 SUBSYSTEM INTERFACES

Table 4: Subsystem interfaces

ID | Description | Inputs | Outputs
#01 | DroneCAN protocol over hardwire connection between GPS module and flight controller | None | Positional data

### 4.4 SPRAYER FIRMWARE MODULE SUBSYSTEM

The sprayer firmware module controls and automates the operation of the drone’s sprayer system based on flight conditions or user commands.

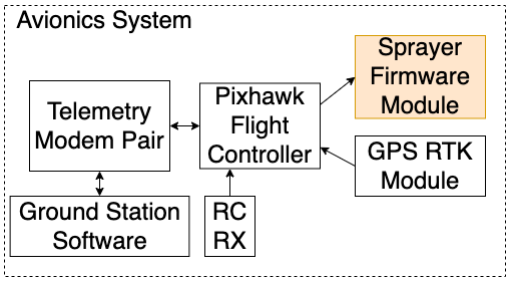
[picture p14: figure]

Figure 6: Avionics system highlighting sprayer modules.

### 4.4.1 ASSUMPTIONS

It is assumed that the sprayer module is compatible with the Cube Orange+ flight controller and receives control commands through standard PX4/ArduPilot interfaces.

### 4.4.2 RESPONSIBILITIES

The sprayer firmware module is responsible for managing the activation of the sprayer pump, typically based on GPS position, altitude, or preprogrammed mission triggers.
It interfaces with the flight controller to receive commands and controls the sprayer hardware accordingly. This subsystem is tightly integrated with the avionics layer for precise, autonomous spraying operations.

### 4.4.3 SUBSYSTEM INTERFACES

Table 5: Subsystem interfaces

ID | Description | Inputs | Outputs
#01 | uORB topic communication between flight controller and sprayer firmware module | Commands | Sprayer control

### 5 POWER AND PROPULSION SYSTEM

The power and propulsion system is a critical system for providing electrical energy to all components of the drone and generating the thrust for flight and maneuverability. This system is composed of the Propulsion Subsystem (motors and electronic speed controllers) and the Power Subsystem (lithiumpolymer battery pack, power distribution board, and Pixhawk power module). The flight controller uses control firmware to command the Propulsion Subsystem, which then drives the motors to achieve desired flight characteristics.

### 5.1 PROPULSION SUBSYSTEM

The Propulsion Subsystem is responsible for generating the thrust needed to lift and maneuver the drone. It consists of the brushless motors and the electronic speed controllers (ESCs) that control them. The arrangement of the four motors, typically in an alternating clockwise and anti-clockwise pattern, helps provide stability by cancelling out net torque.

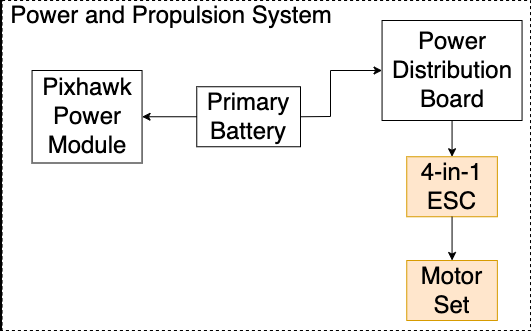
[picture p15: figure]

Figure 7: Propulsion system highlighting motors and ESC

### 5.1.1 ASSUMPTIONS

It is assumed that the ESC firmware is compatible with PX4 Autopilot firmware using the DShot protocol or standard PWM, enabling precise and responsive motor control from the flight controller.

### 5.1.2 RESPONSIBILITIES

It is responsible for providing the necessary thrust for the drone to carry out its mission. The motors need to provide enough thrust to lift the drone, battery, and payload while also being able to fly comfortably in a wide range of weather conditions. The ESCs are responsible for regulating the speed of each motor based on received commands and protecting the motors from overcurrent conditions by limiting power delivery.

### 5.1.3 SUBSYSTEM INTERFACES

Table 6: Subsystem interfaces

ID | Description | Inputs | Outputs
#01 | Hardwire electrical connection be-tween the motor and electronic speed controller. | Electrical power and control signals | Mechanical rota-tion

#02 | Hardwire electrical connection be-tween the motor and LiPo battery | None | None

### 5.2 POWER SUBSYSTEM

The Power Subsystem is responsible for storing and distributing electrical energy to all components of the drone, including the Propulsion Subsystem, Flight Controller, and payload components.

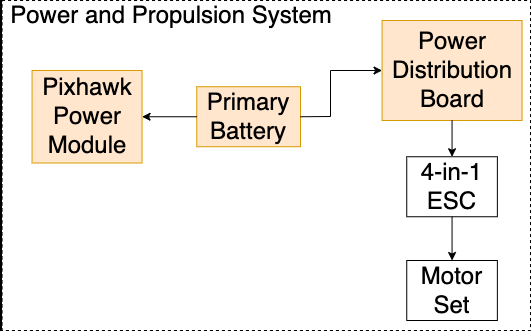
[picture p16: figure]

Figure 8: Propulsion system highlighting power subsystem

### 5.2.1 ASSUMPTIONS

It is assumed that all power components, including the PDB, power module, and ESC, are compatible with PX4 and support XT60 and standard bullet connectors for power distribution.

### 5.2.2 RESPONSIBILITIES

This subsystem is responsible for safely storing electrical energy, providing the necessary voltage and current to operate all drone components, distributing power efficiently through the PDB, and providing voltage and current telemetry data (via the Power Module) to the flight controller.

### 5.2.3 SUBSYSTEM INTERFACES

Table 7: Subsystem interfaces

ID | Description | Inputs | Outputs
#01 | Battery to Pixhawk Power Module | Electrical Power from Battery | Electrical Power to Power Module

#02 | Battery to PDB | Electrical Energy (Stored) | Electrical Power to PDB

#03 | PDB/Power Module to Propulsion Subsystem Power | Electrical Power from Battery | Electrical Power for ESCs/Motors

### 6 CONTROLS SYSTEM

This section provides an overview of the control system, which includes multiple subsysterms for managing both manual and programmatic input. It includes the Radio Control (RC) and Shell Subsystem. The Flight Controls subsystem is responsible for stabilizing and maneuvering the drone, managing pitch, rotation, altitude and roll to ensure smooth flight. Both the RC Subsystem and the Shell Subsystem relay commands to the flight controller, enabling flexible operation modes either manual (via RC) or automated (via command-line interface).

### 6.1 RADIO CONTROL (RC) SUBSYSTEM

The RC subsystem enables manual real-time control of the drone through a physical transmitter and onboard receiver.

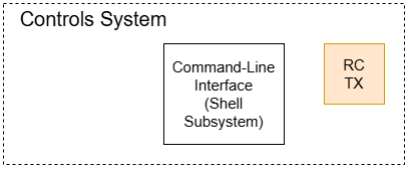
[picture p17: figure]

Figure 9: Controls system highlighting RC subsystem

### 6.1.1 ASSUMPTIONS

The RC system is pre-configured and paired with the drone receiver. Standard 2.4 GHz frequency and channel settings are supported.

### 6.1.2 RESPONSIBILITIES

This subsystem is responsible for transmitting user input to the flight controller to control drone orientation and throttle.It should provide immediate manual override in case of automated mission failure or deviation.

### 6.1.3 SUBSYSTEM INTERFACES

Table 8: Subsystem interfaces

ID | Description | Inputs | Outputs
#04 | RC Tranmission | Manual Joystick Control | Radio signals to receiver

#05 | Receiver to Flight Controller | Electrical connec-tion | PWM/SBUS sig-nals

### 6.2 SHELL SUBSYSTEM

The Shell subsystem provides a programmatic interface for mission automation and direct command-line interaction with the flight controller.

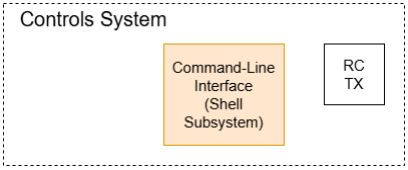
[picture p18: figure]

Figure 10: Controls system highlighting Shell subsystem

### 6.2.1 ASSUMPTIONS

It is assumed that the PX4 firmware with shell access is installed on the flight controller. QGroundControl is used as the primary GCS for interfacing with the Shell subsystem.

### 6.2.2 RESPONSIBILITIES

This subsystem is responsible for executing mission-level scripts and direct commands. It should provide debugging and direct configuration interface for developers or advanced users.

### 6.2.3 SUBSYSTEM INTERFACES

Table 9: Subsystem interfaces

ID | Description | Inputs | Outputs
#06 | Shell Command Input | CLI commands via GCS | Autopilot system instructions

#07 | Shell Telemetry Feedback | Flight controller status | Output to GCS ter-minal

### 7 CAMERA APPLICATION SYSTEM

This section describes the User Interface layer in detail, focusing on its subsystems and their interactions. The layer supports user interaction with the drone system by presenting essential telemetry, navigation, and stability data alongside the real-time camera feed. Each subsystem’s description includes assumptions, responsibilities, and interface details.

### 7.1 VIDEO PROCESSOR SUBSYSTEM

The Video Processor Subsystem is a software component that is designed to control a USB video device, perform image processing, and pass the final video frames to the Graphical User Interface Subsystem. While the core video streaming functionality is handled by the app’s software, additional hardware such as a high-resolution USB camera and a compatible display interface are required to ensure optimal performance. Currently, the Video Processor performs blending algorithms and image format conversion as part of its processing pipeline. Future additions can be made to perform other image processing algorithms due to Video Processor’s modular design.

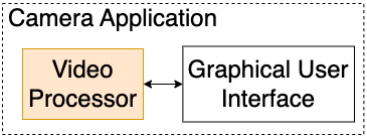
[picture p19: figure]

Figure 11: Camera application system highlighting the video processor subsystem.

### 7.1.1 ASSUMPTIONS

It is assumed that the Video Processor Subsystem will receive a continuous stream of frames from any USB video device. The analog camera used in this project is connected to an analog video capture card which will present the video stream as a digital USB device for the Video Processor Subsystem to process.

### 7.1.2 RESPONSIBILITIES

The Camera Application should capture and stream live video from the drone’s camera to the information overlay for the user. It must minimize latency in the video feed to ensure real-time monitoring capabilities. Additionally, it should allow the selection of various USB video and camera devices and facilitate the superimposition of the crosshair for enhanced targeting accuracy.

### 7.1.3 SUBSYSTEM INTERFACES

Table 10: Subsystem interfaces

ID | Description | Inputs | Outputs
#01 | Video Stream Interface | Camera Transmis-sion | Live video feed to GUI

#02 | Information overlay interface | Video feed Overlay images | Overlay informa-tion and crosshair onto video

### 7.2 GRAPHICAL USER INTERFACE SUBSYSTEM

The GUI Subsystem overlays critical information on the live video feed provided by the Video Processor. Integrates telemetry data (speed, altitude, battery), GPS data, and stability information, visually presenting them to assist navigation. The subsystem includes a built-in crosshair to assist in tracking and alignment of objects during flight operations.

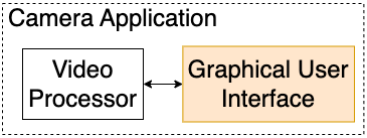
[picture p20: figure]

Figure 12: User interface system highlighting information overlay

### 7.2.1 ASSUMPTIONS

The system is assumed to receive data from the Telemetry Data Source (if the drone is equipped with a telemetry OSD module). If no hardware module exists, then the camera should be able to continue displaying frames with simple overlaid images. The layout can overlay telemetry and other data on top of the video feed without obstructing essential information. Moreover, it is expected that there will be stable integration with the Camera app to display live video alongside other info overlay elements. It can also be assumed that the Video Processor Subsystem will pass frames in order and with lowlatency while receiving input from the Camera System on a perfect medium. The design of the Camera Application will always display a frame, so internal error handling will allow the Video Processor to recover and continue to pass frames to the GUI.

### 7.2.2 RESPONSIBILITIES

It should display the real-time video feed from the Camera app. The system should overlay telemetry data, including speed, altitude, and battery level, on the video feed for user visibility. It should also show GPS and stabilization information as part of the info overlay to assist with navigation and balance monitoring. Crosshair functionality must be integrated to allow users to track targets and enhance their navigation experience.

### 7.2.3 SUBSYSTEM INTERFACES

Table 11: Subsystem interfaces

ID | Description | Inputs | Outputs
#01 | Video Feed Interface | Processed Video Frames | Display Frame on Video Label

### 8 SPRAYER SYSTEM

The Sprayer System enables the controlled delivery of insecticide during drone flight. It is made up of only electrical hardware components that work together to perform precision spraying. This section outlines the assumptions, responsibilities, and interfaces associated with the subsystem.

### 8.1 CONTROL LOGIC VIA FLIGHT CONTROLLER

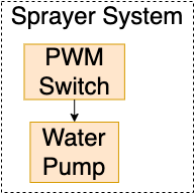
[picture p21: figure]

Figure 13: Sprayer system highlighting PWM-controlled switch and pump

### 8.1.1 ASSUMPTIONS

It is assumed that the flight controller sends a valid PWM signal to the PWM-controlled switch to toggle the electric pump. It is also assumed that the power and ground connections to the pump are stable and correctly configured.

### 8.1.2 RESPONSIBILITIES

The flight controller, via custom firmware, generates high or low PWM signals to toggle the state of the electric pump. When activated, the pump draws insecticide from the reservoir and expels it through the spray nozzle.

### 8.1.3 SUBSYSTEM INTERFACES

Table 12: Subsystem interfaces

ID | Description | Inputs | Outputs
#01 | Pump Activation | PWM signal from flight controller | Pump on/off tog-gle signal

### 9 CAMERA SYSTEM

The Camera System enables real-time video monitoring and navigation of the drone by capturing, transmitting, and digitizing video. It is composed of three subsystems: the FPV Camera, the Video Transmitter, and the Video Capture Subsystem. Together, these components provide operators with a continuous video feed during operation.

### 9.1 FPV CAMERA SUBSYSTEM

The FPV Camera provides real-time video capture from the drone’s perspective. Its primary function is to deliver a continuous video stream that enables operators to visually monitor the drone’s surroundings and identify potential wasp targets. The FPV Camera directly interfaces with the Video Transmission Subsystem, which transmits this live feed to an external receiver, allowing for remote observation and control adjustments based on the visual data.

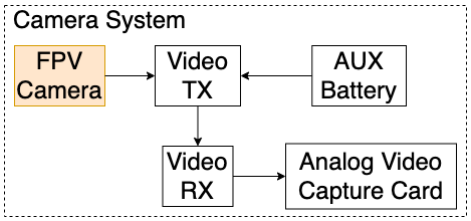
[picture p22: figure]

Figure 14: Camera system highlighting FPV camera

### 9.1.1 ASSUMPTIONS

The FPV Camera provides continuous video streaming and does not perform any image processing.

### 9.1.2 RESPONSIBILITIES

The Video Transmission Subsystem takes the video feed generated by the FPV Camera and transmits it to an external receiver, such as a control station on the ground. This allows operators to monitor the live video stream and make decisions based on the visual data.

### 9.1.3 SUBSYSTEM INTERFACES

Table 13: Subsystem interfaces

ID | Description | Inputs | Outputs
#01 | FPV Camera Output Interface | Power input | Analog video sig-nal

### 9.2 VIDEO TRANSMISSION SUBSYSTEM

The Video Transmission Subsystem sends the video feed to an external receiver. This allows operators to view live footage remotely, enabling real-time response and monitoring during the drone’s operation.

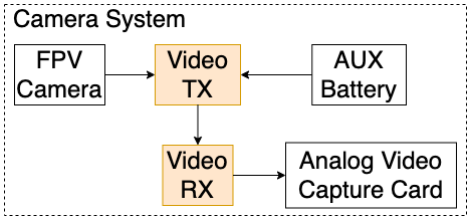
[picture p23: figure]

Figure 15: Camera system highlighting video transmitter

### 9.2.1 ASSUMPTIONS

It is assumed to have a reliable signal range sufficient to transmit live video back to a ground station or monitoring device.

### 9.2.2 RESPONSIBILITIES

The Video Transmitter should take the video feed generated by the FPV Camera and transmit it to an external receiver, such as a control station on the ground. This allows operators to monitor the live video stream and make decisions based on the visual data.

### 9.2.3 SUBSYSTEM INTERFACES

Table 14: Subsystem interfaces

ID | Description | Inputs | Outputs
#01 | Video Transmitter Interface | Video frame NTSC format | Video frame NTSC format (5.8 GHz radio)

### 9.3 VIDEO CAPTURE SUBSYSTEM

The Video Capture Subsystem receives the transmitted analog video via a ground station receiver, digitizes it, and provides it as a USB video input to a Linux device or similar host.

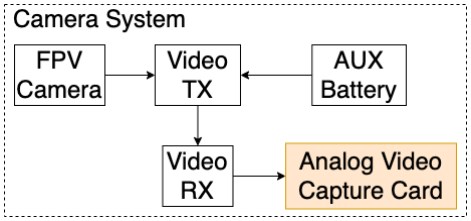
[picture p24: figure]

Figure 16: Camera system highlighting video transmitter

### 9.3.1 ASSUMPTIONS

It is assumed that the host system supports USB Video Class (UVC) devices for video capture functionality. On desktop, the capture card will appear as a USB video device with all of the correct USB headers for that type of device.

### 9.3.2 RESPONSIBILITIES

It is responsible for converting the analog video to digital format using a capture card. It should provide a real-time digital video stream to a user application. Analog to digital conversion is critical as the Camera Application can only interface with USB video devices.

### 9.3.3 SUBSYSTEM INTERFACES

Table 15: Subsystem interfaces

ID | Description | Inputs | Outputs
#01 | Video Digitization Interface | Analog Video (RCA) | Digital Video via USB

REFERENCES

[1] Luis Narez Rajesh Yaksho Nishchal Shrestha Tyler Nguyen, Isaac Medrano. System requirements specifications, 2024.

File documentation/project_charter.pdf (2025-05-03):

## DEPARTMENT OF COMPUTER SCIENCE & ENGINEERING

## THE UNIVERSITY OF TEXAS AT ARLINGTON

## PROJECT CHARTER

# CSE 4316: SENIOR DESIGN I FALL 2024


## VERMINATOR

## WASP DRONE

ISAAC MEDRANO
LUIS NAREZ
TYLER NGUYEN
NISHCHAL SHRESTHA
RAJESH YAKSHO
Verminator - Fall 2024 | page 1 of 15

REVISION HISTORY

Revision | Date | Author(s) | Description
0.1 | 10.01.2024 | TN | Document creation
0.2 | 10.05.2024 | TN, IM | Complete draft
1.0 | 04.29.2025 | TN, RY | Official release

CONTENTS

1 Problem Statement | 6
2 Methodology | 6
3 Value Proposition | 6
4 Development Milestones | 6
5 Background | 7
6 Related Work | 7
7 System Overview | 7
8 Roles & Responsibilities | 9
9 Cost Proposal | 9
10 Facilities & Equipment | 11
11 Assumptions | 11
12 Constraints | 11
13 Risks | 11
14 Documentation & Reporting | 11

LIST OF FIGURES

1 | Overall system diagram showing major systems and their interactions | | 9

### 1 PROBLEM STATEMENT

Wasps pose a risk to many people and can range from simple stings to life-threatening allergic reactions. In many cases, wasp nests can be situated in hard-to-reach areas, making traditional removal methods risky. The goal of this project is to design and build a remote-controlled drone that can assist in the safe removal of wasp and hornet nests.

### 2 METHODOLOGY

For our senior design project, we are developing an integrated system consisting of a drone, remote controller, sprayer system, and desktop camera application to eliminate wasp nests without requiring human contact. The drone is equipped with a low-light, forward-facing camera that transmits a real-time video feed to a ground station. A manual-controlled targeted insecticide delivery system enables the user to neutralize nests from a distance. The system is designed to prioritize safety and environmental responsibility by minimizing collateral impact on non-target species and surrounding areas.

### 3 VALUE PROPOSITION

The value proposition for our wasp-killing drone project offers significant benefits to multiple stakeholders. Our primary stakeholder are homeowners, hobbyists, and small-operation farmers. Commercial drones designed for aerial spraying are prohibitively expensive. In this project, we aim to propose a low-cost alternative using standard, off-the-shelf components that makes it ideal for this type of stakeholder.
Larger, commercial sponsors and stakeholders may also benefit from this project. For applications requiring precise applications of insecticides, this drone’s low-cost and small size allows it to fulfill the role of a precision sprayer that complements much larger and expensive agricultural drones. Academic and industry sponsors can also benefit from this project because it is a modular platform that can be extended to fulfill a wide range of missions.
By supporting this project, sponsors will contribute to the development of a practical, open-source, and low-cost system that addresses important safety concerns.

### 4 DEVELOPMENT MILESTONES

- Project Charter First Draft - September 2024
- System Requirements Specification - September 2024
- Architectural Design Specification - September 2024
- Obtain Major Hardware Components for Drone Platform - December 2025
- Construction of Modular Drone Platform - January 2025
- Detailed Design Specification - February 2025
- Design of Hardware Sprayer Module - February 2025
- Implementation of Hardware Sprayer Module - March 2025
- Implementation of Software Sprayer Module - March 2025
- Design of Live Camera Viewing Software - March 2025
- Implementation of Live Camera Viewing Software - April 2025
- Final Project Demonstration - April 2025

### 5 BACKGROUND

The current methodology for removing wasp nests in homes or small businesses involves soaking the nest in insecticide or using foaming sprays at the opening of the wasp nest. This can pose several issues. First, wasp nests can be located in hard-to-reach areas, requiring the use of ladders, which can be risky for those attempting to remove wasp nests. Second, both methods require someone to be within close proximity to the wasp nest which raises safety and health concerns. This project seeks to address these challenges by providing a solution that allows customers to safely remove wasp nests from a distance. This project is sponsored by Dr. Shawn Gieser and Dr. Chris McMurrough. The target customers are exterminators, homeowners, businesses, and drone hobbyists. The motivation behind this project arises from health concerns and general dislike of being stung by wasps. There is an existing relationship between the development team and potential customers, as the team members themselves could serve as early adopters of this product.

### 6 RELATED WORK

There are few commercial solutions to remove wasp nests using drones; however, the idea of using a drone as a spraying platform is not new. In recent years, drones have been used in the agriculture industry to spray pesticides, herbicides, and fertilizers on crops. DJI, a Chinese company known for designing drones and cameras, have a lineup of agricultural drones for this purpose [1]. DJI went on to publish an industry report noting the potential for growth in their agricultural drone business with over 300,000 units sold [2]. Moreover, large heavy-lift drones has been demonstrated as successful in academia. The Freyr Drone project by Spoorthi et al. have demonstrated the feasibility of drones to distribute pesticides and fertilizers in crop fields [3].
Previous Fall 2023 senior design 1 team at the University of Texas at Arlington worked on a drone for the Raytheon Drone Competition. The project involved developing an autonomous drone (UAV) to identify and target unfriendly ground vehicles (UGVs) using water blasts. The UAV used LiDAR and computer vision to achieve this. Their system specifications are outlined in their project charter.
Our product will be adjacent work to products similar to DJI’s agricultural drones, but instead of focusing on the agricultural application of drones only, we aim to investigate applications for homes and businesses with a much more affordable price point.

### 7 SYSTEM OVERVIEW

At a high level, the major components of the product will include the drone platform, a desktop application to capture video stream from a first-person camera on the drone, custom firmware to control the water sprayer, and the hardware components that make up the sprayer itself. The user will control the drone using a remote controller, and the desktop application will be used to receive and display the video feed from the first-person camera. These components are organized into the following systems:

- Avionics System
- Controls System
- Sprayer System
- Camera Application System
- Power and Propulsion System
- Camera System

### 7.1 AVIONICS SYSTEM

The Avionics System serves as the "brain" of the drone. All commands for the drone and sprayer are first sent to the Avionics System for processing. This processing occurs at the flight controller. The chosen flight controller is a Pixhawk-compliant CubePilot Cube Orange+ running the PX4 Autopilot Firmware. After the flight controller processes commands, the messages, signals, or other commands are sent to other hardware components to perform a task. The Avionics Systems also contains other subsystems in charge of telemetry, positioning of the drone, and ensuring the drone can communicate with ground station software.

### 7.2 CONTROLS SYSTEM

The Controls System allows the user or pilot to interact with the drone. The Controls System allows the user to use both a command-line interface or RC controller. The RC controller interacts directly with the hardware through the flight controller and dedicated RC receiver. The command-line interface allows the drone to be configured to operate programmatically, enabling future automation if desired.

### 7.3 SPRAYER SYSTEM

The Sprayer System will be the first payload device designed for the Verminator Wasp Drone platform. With the Sprayer System attached, the drone’s mission is to spray insecticides at wasp nests. This will be carried out using a liquid pump and spray nozzle. The liquid pump is to be toggled with a PWM-controlled switch. The PWM-controlled switch is operated by the flight controller. An onboard software module in the firmware toggles the switch programmatically, or the RC controller can toggle the switch through the RC receiver and flight controller directly.

### 7.4 CAMERA APPLICATION SYSTEM

A software application to display the live video feed from the drone’s camera will be developed alongside the drone. The purpose of this application is to provide the user with information overlays, a targetting crosshair, and live video. This system will allow the user to fly the drone in tight spaces, or in spaces that are outside the line-of-sight of the user.

### 7.5 POWER AND PROPULSION SYSTEM

This system will provide the drone with necessary thrust to lift itself and its payload to fulfill its mission. The drone is designed as a 3S LiPo system giving it a wide-range of hardware to pick from. Other functions of the Power and Propulsion System is to provide sufficient power to other components of the drone and payload.

### 7.6 CAMERA SYSTEM

The Camera System will provide the Camera Application System with a wide-angle, low-light capable, first-person view from the drone’s perspective. This will allow the user to fly the drone in a wide-range of conditions, times, and continue to fly when the drone is out of the pilot’s visual field.


Figure 1: Overall system diagram showing major systems and their interactions.

### 8 ROLES & RESPONSIBILITIES

The stakeholders for this project are Dr. Shawn Gieser and Dr. Chris McMurrough. The point of contact will be Dr. Gieser.
The team members are Isaac Medrano, Luis Narez, Tyler Nguyen, Nishchal Shrestha, and Rajesh Yaksho. Tyler Nguyen will be the product owner and scrum master for the duration of the project. The following list lists the role of each team member with regard to their project contributions:
- Tyler Nguyen: Team lead, software engineer, hardware engineer
- Isaac Medrano: Software engineer, artist
- Rajesh Yaksho: Software engineer
- Luis Narez: Software engineer
- Nishchal Shrestha: Softrware engineer

The software engineers on the project are tasked with developing the live camera application. The hardware engineers are responsible for the design and construction of the drone, and implementing firmware modifications. The artist is tasked with producing images to overlay for video processing and the team logo.

### 9 COST PROPOSAL

### 9.1 PRELIMINARY BUDGET

The majority of the budget will be spent on the drone. Software is free and open source under BSD 3-Clause and MIT Licenses, so no budgeting is required.

Item | Estimated Cost (USD)
500-X4 500mm Quadcopter frame | 76
3S 5200mAh 11.1v LiPo battery | 35
XT60 battery connectors | 9
Deans female to XT60 male adapter | 8
XT60 12AWG | 9
XT60 14AWG | 9
CubePilot Cube Orange+ with ADS-B Carrier Board | 385
Here3 GNSS | 225
RFD900x U.S. Telemetry Modem Set | 130
Readytosky 2212 920KV Brushless Motors CW CCW | 40
Diatone Mamba 40A Brushless 4-in-1 ESC F40B LSDsho t60040A3 − 6S | 100
1045 propeller pack | 17
6-12V DC Water Pump | 10
1/4" ID 3/8" OD Silicon Tube | 10
3/8" OD Bulkhead Fitting | 7
1/4" Barbed Fitting to 1/4" Female NPT Adapter | 7
1/4" Male NPT Srpay Nozzle 60 degree Cone Brass | 15
DC 5V-12V 20A PWM Switch | 9
10oz/300mL HDPE Bottle | 13
RunCam Night Eagle 3 | 70
5.8 GHz 600mW Analog Video Transmitter | 34
RC832S 5.8 GHz Analog Video Receiver | 28
Analog Video Capture Card | 13
450 mAh 3s LiPo Battery | 16
FrSky Taranis 2.4 GHz Q X7 Transmitter | 124
FrSky Taranis 2.4 GHz X8R Receiver | 39
M3 Screws Steel | 8
M2.5 Screws Steel 3 | 12
2.54mm Dupont Connector Set | 10
Rubberized Battery Straps | 17
12 AWG Wire | 13
16 AWG Wire | 17
Anti-Vibration Balls | 7
3M Adhesive Backed Hook and Loop Fastener | 12
Zip Ties | 6

Table 1: Preliminary Cost Estimates

### 9.2 CURRENT & PENDING SUPPORT

Funding for this project will be provided by the Department of Computer Science and Engineering and the development team. Total support for this project by the CSE department is 800 USD. If more funding is needed, the development team will have to source funding. Additional funding can come from unused budgets from other senior design teams.

### 10 FACILITIES & EQUIPMENT

The University will provide accesses to Labs 208 and 241 which contain the drone space needed to test drone flight with drone netting for safety, as well as store parts for the drone. The University will also provide the outdoor space needed to field test the drone. We will have to source the venom delivery mechanism and the venom itself. These parts can be bought at local utility stores or online. Existing venom delivery methods include water pumps, venom spray cans, and agriculture drone attachments. We will also require a camera and controller which will be purchased from online sources.

### 11 ASSUMPTIONS

The following list contains critical assumptions related to the implementation and testing of the project.

- A safe lab environment will be available for building and testing the drone and its features.
- All necessary sensors and electronic devices will receive approval and be available in a timely manner for integration into the project.
- The power supply and weight distribution of the drone will function as planned, ensuring stable flight and the effective operation of all sensors.
- All the components required for the project will be within our budget.
- All features outlined in the requirements will be completed before the prototype demo.
- Help from professor and lab technician will be available for completion of this project.

### 12 CONSTRAINTS

The following list contains key constraints related to the implementation and testing of the project.

- Final prototype demonstration must be completed by May 1st, 2025.
- Testing to be conducted only in a safe lab environment.
- The drone for this project must be built; a pre-built drone cannot be purchased.
- Total development costs must not exceed $800.
- Use of actual insecticides is prohibited.

### 13 RISKS

The following high-level risk census contains identified project risks with the highest exposure. Mitigation strategies will be discussed in future planning sessions.

### 14 DOCUMENTATION & REPORTING

### 14.1 MAJOR DOCUMENTATION DELIVERABLES

### 14.1.1 PROJECT CHARTER

Maintenance of the Project Charter will be a shared responsibility among all team members. It will serve as a stable document, subject to be updated only under significant changes such as regulatory modifications, new lessons learned, or substantial alterations in project scope. The initial version is expected by September 23, 2024, and the final version, along with a project demo video, will be delivered at project completion.

Risk description | Probability | Loss (days) | Exposure (days)
Availability of specific drone components from approved vendors | 0.50 | 21 | 10.5
Delays in shipping of the ordered parts for the drone | 0.10 | 14 | 1.4
Approval/Registration from FAA if the weight of drone exceeds 250gm | 0.20 | 7 | 1.4
Compatibility issue between chosen hardware and software requirement | 0.40 | 21 | 8.4
Problem with weight distribution affecting flight performance | 0.40 | 14 | 5.6
Issues with battery life limiting drone operation time | 0.10 | 7 | 0.7
Camera system/targeting mechanism could malfunction | 0.20 | 21 | 4.2

Table 2: Overview of highest exposure project risks

### 14.1.2 SYSTEM REQUIREMENTS SPECIFICATION

The SRS will be maintained using Overleaf for collaborative LaTeX editing. There will be updates only if major changes occur in the development process or if new features are required by the sponsor. The first version will be delivered in October 2024, with the final version targeted for November 2024.

### 14.1.3 ARCHITECTURAL DESIGN SPECIFICATION

Each team member will contribute individually to maintaining the document. Updates will be made regularly as drone improvements and modifications occur throughout the project. The focus will be on key components such as flight control systems, the payload system (water container), and navigation mechanisms that will be operated through a desktop app.

### 14.1.4 DETAILED DESIGN SPECIFICATION

The DDS will be reviewed and updated after Sprint 3 to ensure alignment with the evolving project and design changes. Significant updates will occur in response to major revisions in technical architecture, drone design, or new requirements from stakeholders. The lead drone engineer will be responsible for updates, under the supervision of the project manager. The first version will be delivered before Sprint 4, and a final version will be delivered closer to project completion.

### 14.2 RECURRING SPRINT ITEMS

### 14.2.1 PRODUCT BACKLOG

Backlog items will be derived from the SRS, with additional input from the project team and sponsor. Requirements such as drone autonomy, water deployment, and structural integrity will be broken into Jira tasks and prioritized by the product owner.

### 14.2.2 SPRINT PLANNING

There will be 6 - 8 sprints, depending on the overall timeline and deliverables. For each sprint, the team will define specific sprint goals, select backlog items, and assign tasks based on team capacity. Feedback from stakeholders will help shape each sprint plan.

### 14.2.3 SPRINT GOAL

Sprint goals will focus on achieving milestones such as drone prototype assembly, development of the desktop application, and integration of waster dispensing mechanism. These goals will be refined through regular feedback from instructors and the project sponsor.

### 14.2.4 SPRINT BACKLOG

Items from the product backlog for each sprint will be selected based on sprint priorities and feasibility. The sprint backlog will include drone hardware components, software modules, and safety testing procedures. Jira will be used to track progress and make necessary updates.

### 14.2.5 TASK BREAKDOWN

Tasks will be claimed by team members at the start of each sprint, with remaining tasks assigned as necessary. Responsibilities will include areas such as hardware assembly, coding the drone control desktop app, and ensuring pesticide safety and containment.

### 14.2.6 SPRINT BURN DOWN CHARTS

Sprint progress will be tracked using burn down charts in Jira and the provided Excel spreadsheet, providing a visual representation of remaining work. The team will review these charts at the end of each sprint to adjust plans and timelines.

### 14.2.7 SPRINT RETROSPECTIVE

At the end of each sprint, the team will conduct a retrospective, led by the rotating scrum master. This will allow for collective feedback, process improvement, and planning for the next sprint.

### 14.2.8 INDIVIDUAL STATUS REPORTS

Each team member will submit a PDF report detailing their sprint goals, completed tasks, time spent, and feedback. This report will be reviewed by the team instructor and sponsor.

### 14.3 CLOSEOUT MATERIALS

### 14.3.1 SYSTEM PROTOTYPE

The prototype demonstration will feature an unmanned drone deploying water onto a simulated wasp nest. The demo will occur on-site at an approved testing facility. Project acceptance will based on the evaluation of sponsors on drone’s accuracy and functionality.

### 14.3.2 PROJECT POSTER

The poster will summarize the goals, methodology, design, and the real-world application of the project. It will be presented during the final demo in April 2025.

### 14.3.3 WEB PAGE

A GitHub repository will host web page of the project. It will contain a Read-Me, along with a demonstration video of the drone in action, and other documentation. The page will be made public after the project completion.

### 14.3.4 DEMO VIDEO

Two demo videos will be produced: one after the initial prototype is complete and the final video showing the full capabilities of the drone in neutralizing a wasp nest using the app control.

### 14.3.5 SOURCE CODE

The source code for the drone’s software, including its autonomous flight controls and water sprayer system, will be stored in a GitHub repository under an MIT license, or other licenses as required by existing open source projects.

### 14.3.6 SOURCE CODE DOCUMENTATION

All source code documentation will be generated and edited using Doxygen. A final documentation file will be included in the GitHub repository as PDF and HTML.

### 14.3.7 CAD FILES

Mechanical designs for various components of the project will be developed using Autodesk AutoCAD. To prototype and test these designs, 3D printing will be used. All CAD files will be provided throughout the duration of this project.

### 14.3.8 INSTALLATION SCRIPTS

Installation instructions will be available in the Read-Me section of the GitHub repository, guiding users through setting up the drone’s software environment and the desktop camera application.

### 14.3.9 USER MANUAL

The user manual, available in the Read-Me, will explain how to configure the drone’s environment and launch an unmanned flight for nest elimination using remote controller and the camera app on desktop.

REFERENCES

[1] DJI. DJI Agriculture.
[2] DJI. Agricultural Drone Industry Insight Report, 2023.
[3] Spoorthi S. et al. Freyr drone: Pesticide/fertilizers spraying drone - an agricultural approach. In International Conference on Computer and Communications Technologies (ICCCT), 2017.

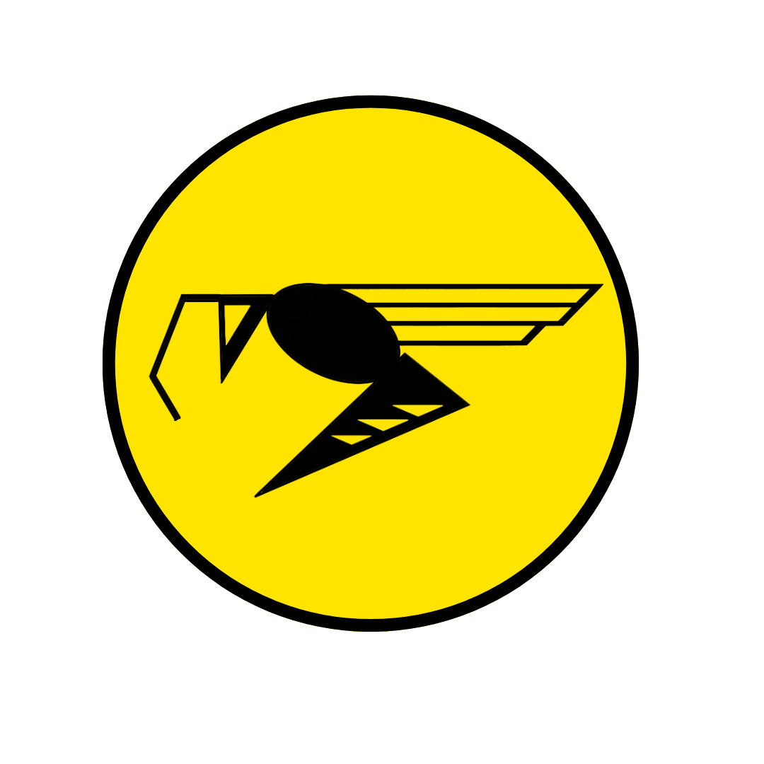
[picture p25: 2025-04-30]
resources/images/verminator_emblem.png

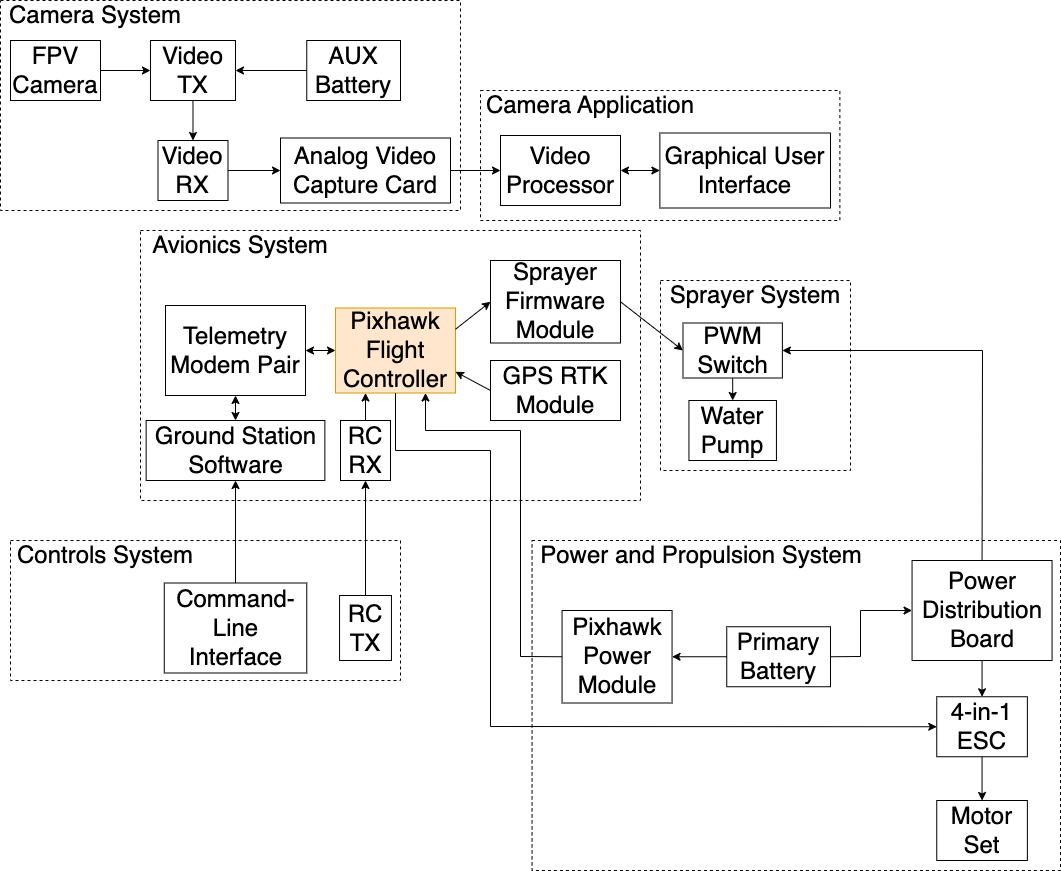
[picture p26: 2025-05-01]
resources/images/ads_r2_full.png

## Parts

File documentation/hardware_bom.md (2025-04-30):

# Bill of Materials (BoM)

## Airframe components
[500-X4 500mm Quadcopter frame](https://www.amazon.com/FPVKing-500-X4-Quadcopter-Upgrade-Landing/dp/B087LT81C8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) (QTY 1)

## Power components
[3S 5200mAh 11.1v LiPo battery](https://a.co/d/6rPRNIA) (QTY 1)

[XT60 battery connectors](https://a.co/d/amNlAyu) (QTY 1)

[Deans female to XT60 male adapter](https://a.co/d/5JDpXND) (QTY 1)

[XT60 12AWG](https://www.amazon.com/Pairs-Female-Connector-Silicon-Battery/dp/B07QH249CR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) (QTY 1, Set of 3 pairs)

[XT60 14AWG](https://www.amazon.com/Pairs-Connector-Female-Silicon-Battery/dp/B085HF31K7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) (QTY 2, Set of 5 pairs)

## Avionics
### Flight Controller
[CubePilot Cube Orange+ with ADS-B Carrier Board](https://irlock.com/products/cube-orange-plus-standard-set)
### RTK GPS Module
Here3 GNSS (Provided by the Department of Computer Science and Engineering)
### Telemetry Radio
RFD900x U.S. Telemetry Modem Set (Provided by the Department of Computer Science and Engineering)

## Propulsion
### Motors
[Readytosky 2212 920KV Brushless Motors CW CCW](https://www.amazon.com/Readytosky-Brushless-Motors-Phantom-Quadcopter/dp/B075DD16LK) (QTY 1, Set of 4)
### ESC
[Diatone Mamba 40A Brushless 4-in-1 ESC F40_BLS Dshot600 40A 3-6S](https://speedyfpv.com/products/diatone-mamba-40a-brushless-4-in-1-esc-f40_bls-dshot600-40a-3-6s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) (QTY 1)
### Propeller
[1045 propeller pack](https://www.amazon.com/dp/B0823NNTKD?psc=1&ref=ppx_yo2ov_dt_b_product_details) (QTY 1, Set of 12)

## Payload
[6-12V DC Water Pump](https://www.amazon.com/Gikfun-Aquarium-Cooled-Diaphragm-EK1856/dp/B0744FWNFR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)

[1/4" ID 3/8" OD Silicon Tube](https://www.amazon.com/Silicon-JoyTube-Silicone-Brewing-Winemaking/dp/B07W5TGX8B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) (QTY 1, 10')

[3/8" OD Bulkhead Fitting](https://www.amazon.com/PureSec-Connect-Plastic-Bulkhead-adapter/dp/B079KQ557Z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) (QTY 1, Set of 5)

[1/4" Barbed Fitting to 1/4" Female NPT Adapter](https://www.amazon.com/PureSec-Connect-Plastic-Bulkhead-adapter/dp/B079KQ557Z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) (QTY 1, Set of 2)

[1/4" Male NPT Srpay Nozzle 60 degree Cone Brass](https://www.mcmaster.com/32885K153/) (QTY 1)

[DC 5V-12V 20A PWM Switch](https://www.amazon.com/5V-12V-Switch-Controller-Control-Lights%EF%BC%88Black/dp/B0CDFL5VVQ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) (QTY 1)

[10oz/300mL HDPE Bottle](https://www.amazon.com/5V-12V-Switch-Controller-Control-Lights%EF%BC%88Black/dp/B0CDFL5VVQ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) (QTY 1, Set of 4)

## Video Components
[RunCam Night Eagle 3](https://www.amazon.com/RunCam-Night-Camera-1000TVL-Support/dp/B09JVG2D5W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) (QTY 1)

[5.8 GHz 600mW Analog Video Transmitter](https://www.amazon.com/AKK-Degree-800TVL-Switchable-Transmitter/dp/B01N48QUIP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) (QTY 1)

[RC832S 5.8 GHz Analog Video Receiver](https://speedyfpv.com/products/rc832s-5-8ghz-av-fpv-receiver-48-channel-7-26v-with-cables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) (QTY 1)

[Analog Video Capture Card](https://www.amazon.com/Capture-Converter-USB-Convert-Camcorder-Compatible/dp/B0CB6BW6X4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) (QTY 1)

[450 mAh 3s LiPo Battery](https://www.amazon.com/TATTU-450mAh-Battery-Torrent-Flite/dp/B0714GN73V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) (QTY 1)

## RC Components
[FrSky Taranis 2.4 GHz Q X7 Transmitter](https://www.amazon.com/FrSky-2-4GHz-Taranis-Access-Transmitter/dp/B08689K3BM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) (QTY 1)

[FrSky Taranis 2.4 GHz X8R Receiver](https://www.amazon.com/FrSky-Taranis-Compatible-Receiver-8-Channel/dp/B00RCAHHFM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) (QTY 1)

## Miscellaneous
M3 Screws Steel (Provided by the Department of Computer Science and Engineering)

[M2.5 Screws Steel](https://www.amazon.com/Assortment-Stainless-Replacement-Machine-Fastener/dp/B0CRRCYZHS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) (QTY 1)

[2.54mm Dupont Connector Set](https://www.amazon.com/Taiss-Connector-Housing-Adaptor-Assortment/dp/B0B11SX39B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) (QTY 1)

[Rubberized Battery Straps](https://www.amazon.com/Apex-RC-Products-Rubberized-Non-Slip/dp/B01F7MEDW6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) (QTY 1, Set of 5)

12 AWG Wire (Provided by the Department of Computer Science and Engineering)

16 AWG Wire (Provided by the Department of Computer Science and Engineering)

[Anti-Vibration Balls](https://www.amazon.com/dp/B073LPTHCL?_encoding=UTF8&psc=1&ref_=cm_sw_r_cp_ud_dp_WQJ314N7MB5YKV9JEKTD) (QTY 1)

3M Adhesive Backed Hook and Loop Fastener (Provided by the Department of Computer Science and Engineering)

Zip Ties (Provided by the Department of Computer Science and Engineering)

## Costs
A lot...

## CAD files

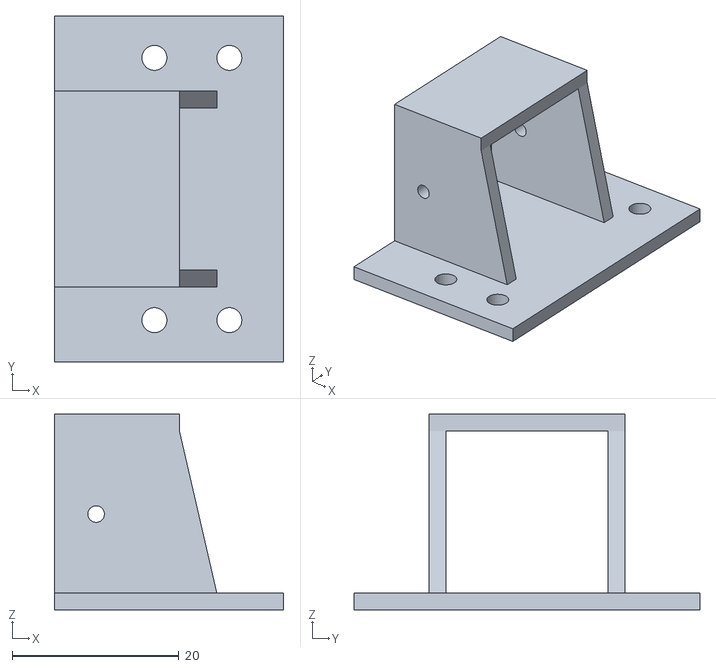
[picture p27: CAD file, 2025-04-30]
resources/cad/camera_mount_r4 v1.stl
27.5 x 41.5 x 23.5

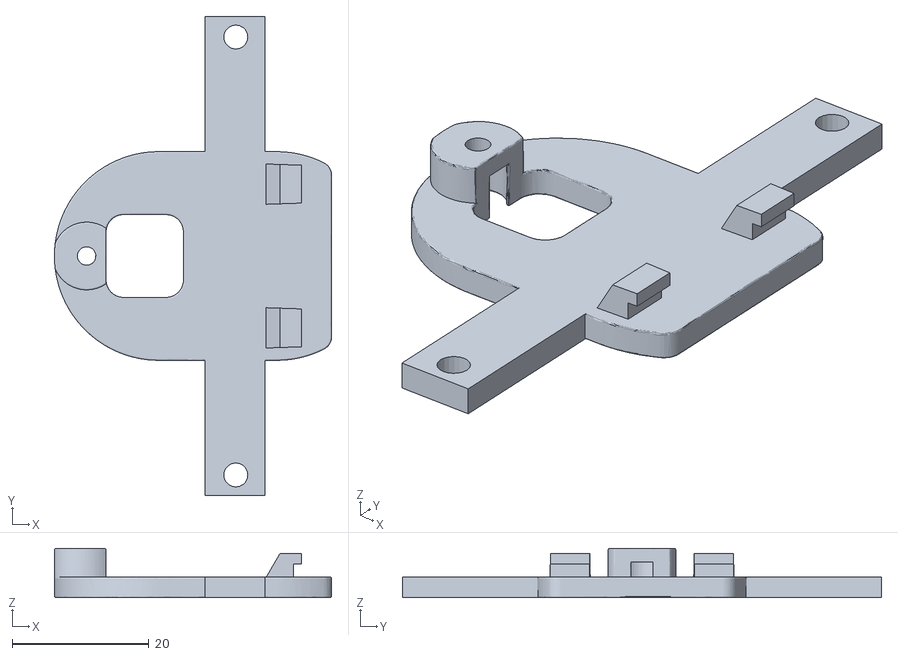
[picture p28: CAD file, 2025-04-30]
resources/cad/Here3 straddle mount.stl
40.5 x 70.0 x 7.20

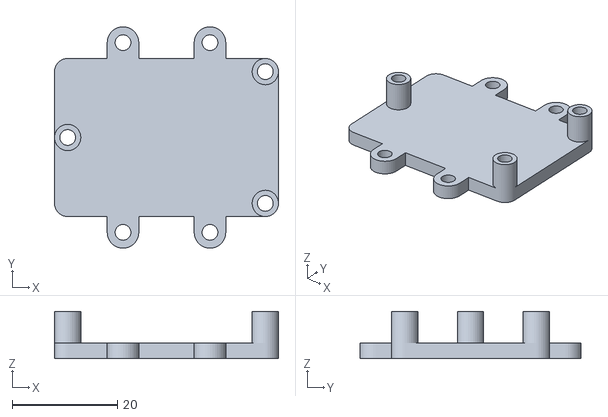
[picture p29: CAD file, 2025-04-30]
resources/cad/rfd_900x_mount v4.stl
42.5 x 42.0 x 9.00

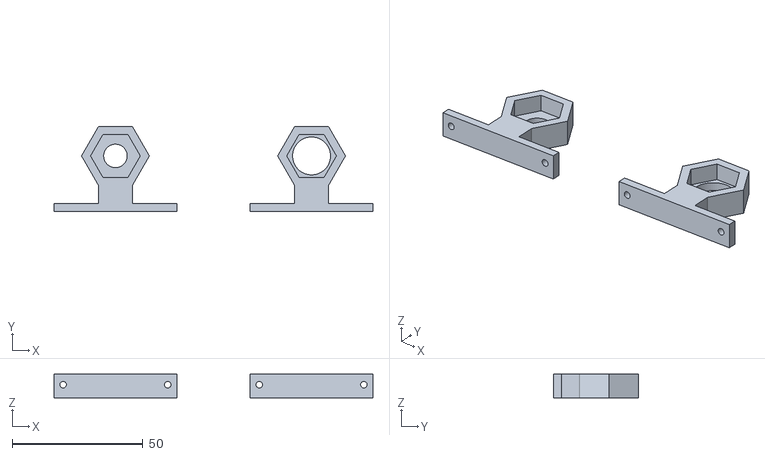
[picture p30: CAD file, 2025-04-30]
resources/cad/nozzle_mount_r1 v1.stl
122.0 x 32.5 x 9.00

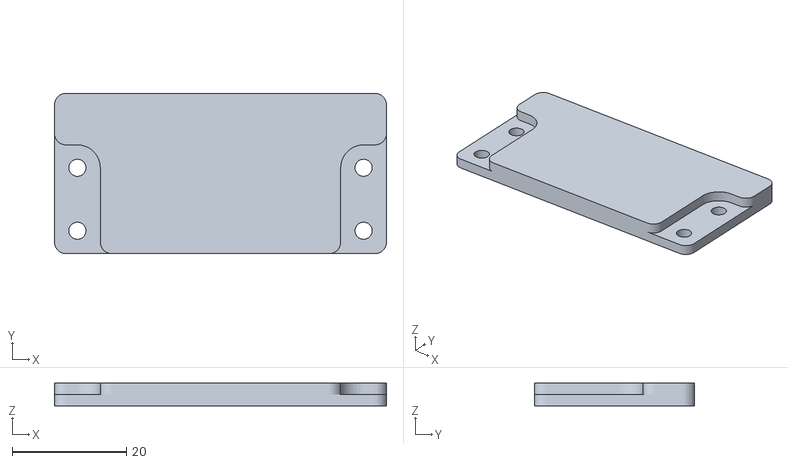
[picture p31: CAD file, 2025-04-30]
resources/cad/adhesive_frame_mount v1.stl
58.0 x 28.0 x 4.00

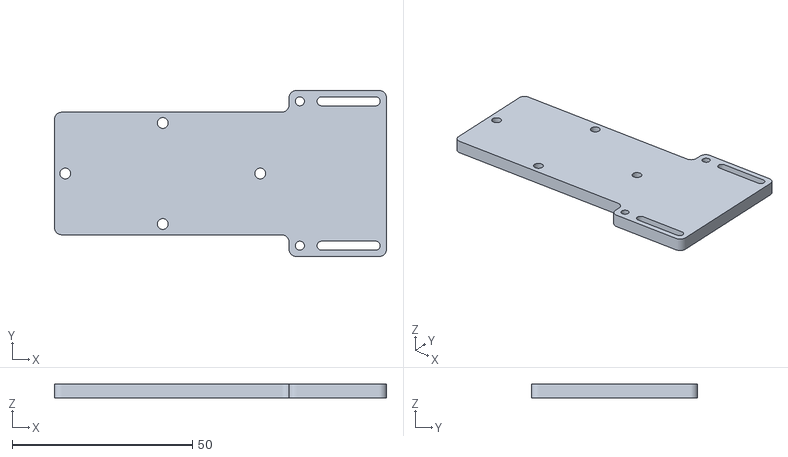
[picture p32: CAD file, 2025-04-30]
resources/cad/nozzle_subframe_mount v4.stl
92.0 x 46.0 x 4.00

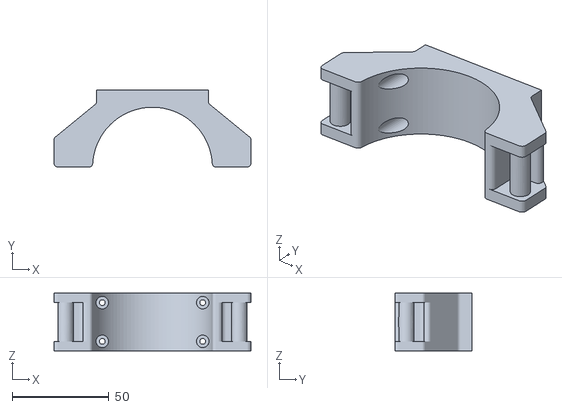
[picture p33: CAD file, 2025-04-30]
resources/cad/tank_mount v8.stl
102.0 x 40.0 x 30.0

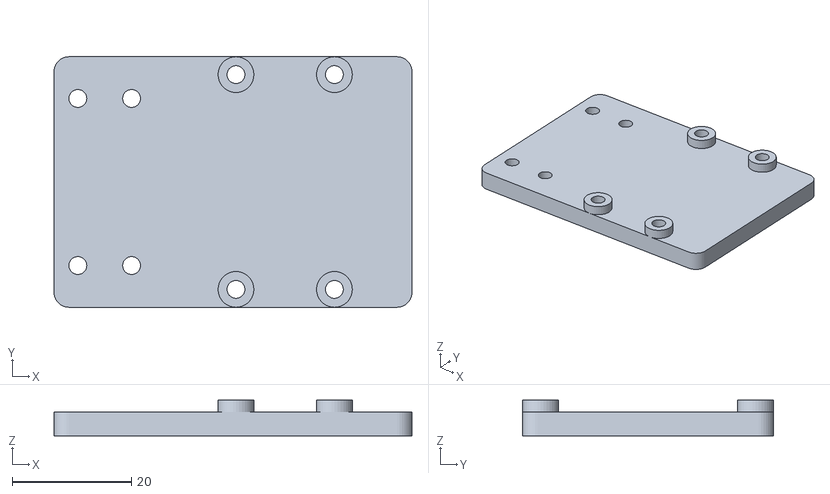
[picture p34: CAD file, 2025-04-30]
resources/cad/modem_frame_mount v3.stl
60.0 x 42.0 x 6.00

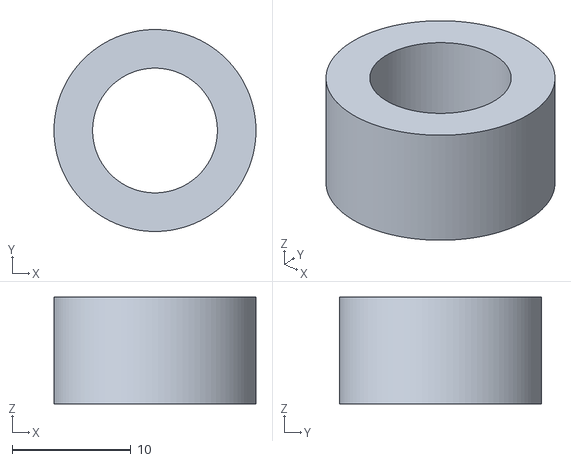
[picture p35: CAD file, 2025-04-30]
resources/cad/rail_spacer v2.stl
17.0 x 17.0 x 9.00

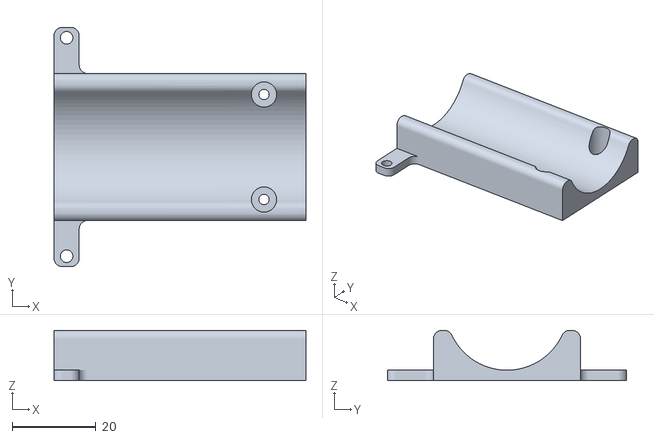
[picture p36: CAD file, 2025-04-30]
resources/cad/water_pump_mount_r5 v7.stl
60.0 x 57.0 x 12.0

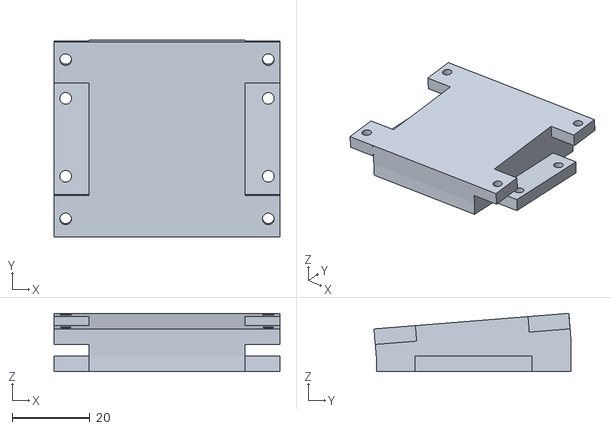
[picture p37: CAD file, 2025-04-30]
resources/cad/tank_angled_mount v2.stl
58.0 x 50.6 x 15.0

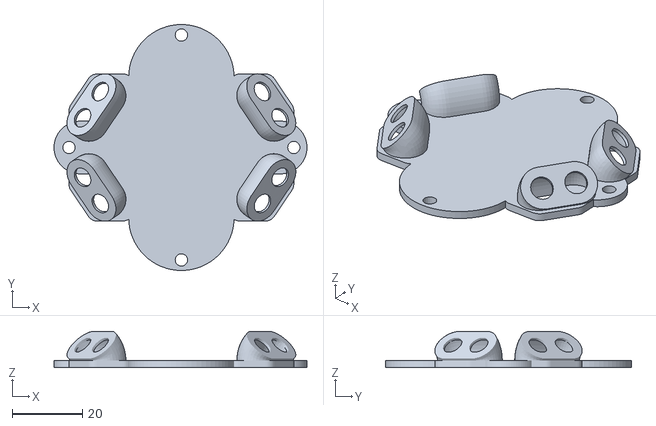
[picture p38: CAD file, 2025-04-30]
resources/cad/S550 CubeOrange vibration mount - BOTTOM.stl
72.0 x 70.0 x 10.4

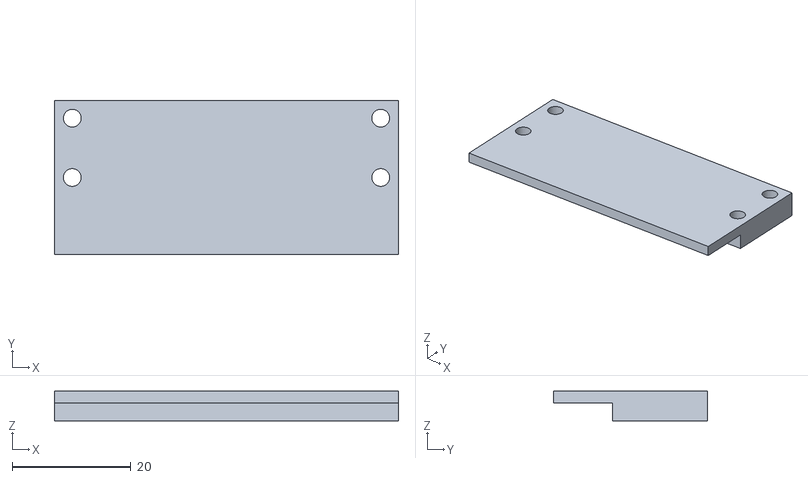
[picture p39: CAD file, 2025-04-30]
resources/cad/aux_battery_mount v4.stl
58.0 x 26.0 x 5.00

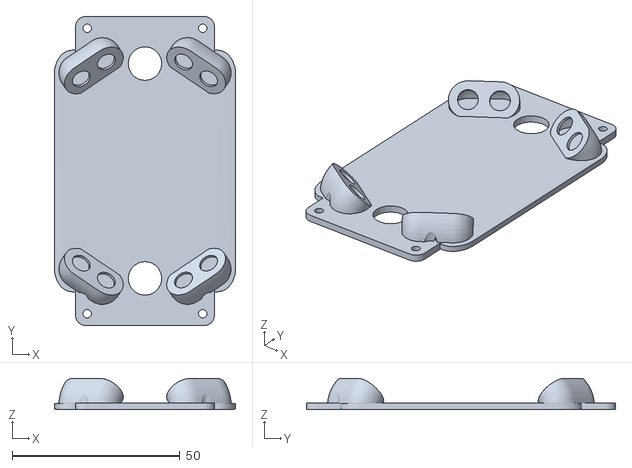
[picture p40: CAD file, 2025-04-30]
resources/cad/S550 CubeOrange vibration mount - TOP.stl
54.0 x 92.1 x 9.35

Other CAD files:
resources/cad/vtx_mount_r4 v2.stl
resources/cad/battery_mount r2 v2.stl

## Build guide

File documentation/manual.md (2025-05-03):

# Verminator Wasp Drone Manual

## Setting Up a Development Environment
To configure your system for development purposes, traverse to the desired directory to store this project. Then clone the repository:
```
    cd path/to/desired/location
    git clone git@github.com:nguyent11/verm-wasp-drone.git
    cd verm-wasp-drone
```

This project links other repositories as submodules. To clone the submodules, run the following command:
```
    git submodule update --init --recursive
```

## Hardware
This manual mainly covers instructions regarding the operation of the hardware. For more information on hardware implementations, take a look at the [Detailed Design Specification](https://github.com/nguyent11/verm-wasp-drone/blob/main/documentation/detailed_design_specification_r2.pdf) document for design and implementation details.

### Connecting the Drone to Ground Station Software
The drone's flight controller is loaded with PX4 Autopilot Firmware. QGroundControl (QGC) is a ground station software that is fully compatible with PX4 drones. To connect the drone to QGC, simply turn power on the drone. The connection should occur automatically.

If the connection is not automatic, calibrating the telemetry radios will be necessary. Refer to RFDesign RFD 900x-US [documentation](https://files.rfdesign.com.au/docs/) on how to calibrate a pair of telemetry modems.

### Uploading Custom Firmware to the Drone's Flight Controller
PX4 Autopilot makes it simple to compile new firmware modifications. This drone uses the CubePilot Cube Orange+ flight controller. To target this platform, use:
```
    make cubepilot_cubeorangeplus
```

After compiling the new firmware, firmware can be uploaded to the drone through QGroundControl. Connect the flight controller to the ground station computer using a Micro USB to USB cable. Under vehicle settings and under firmware, a custom install can be selected. When performing a custom install, select the modified firmware desired, then flash the firmware. Refer to [PX4 developer's documentation](https://docs.px4.io/main/en/development/development.html) on how to build PX4 software or setup a development environment for more information.

If you are not developing for the drone, but for whatever reason, lost the firmware for the flight controller, the firmware can be rebuilt from this repository. Traverse starting from the root of the repository and going to src/drone_firmware/ and enter the following command:
```
    bash build.sh
```

### Preparing for Flight
Before flight can begin, a preflight check is required. QGroundControl will notify the user of required tests before the drone can be armed. Refer to [PX4](https://docs.px4.io/main/en/advanced_config/prearm_arm_disarm.html) and [QGC](https://docs.qgroundcontrol.com/Stable_V4.3/en/qgc-user-guide/fly_view/fly_view.html) documentation on information regarding pre-flight checks and ground control software.

It may also be useful for the user to set up their RC transmitter and controller with predefiend switch assignments. Instructions on how to do this vary by manufacturer. Refer to your RC controller's manual on more information on how to do this. To bind RC switches in QGroundControl, they can be found on the radio and actuator sections of Vehicle Setup. The Vermiantor Team recommends setting a switch for arming/disarming the drone and second switch for toggling the sprayer.

Before flying, attaching the drones propellers are necessary. The motors spin in one of two directions, so ensuring that the propellers are located in the correct orientation is required. The propellers will have a lock symbol with an arrow pointed in a certain direction. The silver nut motors spin CCW. The black nut motors spin CW. Ensure that the propellers are attached to the correct motor. To do so, make sure that the nut to lock the propeller spins in the same diretion that the propeller is labelled with.

If this is the first time flying, calibrating the electronic speed controllers (ESCs) and battery is required. Refer to [PX4 documentation](https://docs.px4.io/main/en/config/actuators.html) to calibrate ESCs and motors.

### Flying the Drone
To arm the drone, ensure that the throttle is placed at the lowest positon. If RC switches are configured, flip the switch to arm the drone. If RC switches are not configured, click arm and slide the arm slider in QGroundControl.

When the drone is armed, the motors and propellers should be spinning at a low speed. Increase thrust by pushing the throttle upwards. The following table lists flight controls for the drone:
| Rotation Type | Stick Control |
| --- | --- |
| Pitch | Right stick up/down |
| Yaw | Left stick left/right  |
| Roll | Right stick left/right |

### Controlling the Sprayer
Because the sprayer is defined as a motor, controlling it requires the drone to be armed. If the drone is flying, it is already armed. If the drone is not flying, arm the drone.

There are two methods of toggling the sprayer:
1. If the RC switch for the sprayer is configured, flip the switch and the sprayer will turn on through hardware. Return the switch to the normal position to stop spraying.
2. If the RC switch for the sprayer is not configured, enter the drone's shell in QGroundControl. It is under Analytical Tools. Enter command `sprayer start` to toggle the sprayer on. Enter command `sprayer stop` to toggle the sprayer off.

### Filling the Insecticide Tank
The tank uses a standard 12V liquid pump. Do not toggle the pump without liquid. Liquid is used to cool the pump's internals.

To fill the liquid insectide tank, unscrew the tank from the cap and silicone tube assembly. Fill the tank with liquid insecticide. Screw the tank back onto the cap and silicone tube assembly. Ensure that the straw is rotated downwards by turning the insecticide tank in its mount. Once the tank is in positon, tighten the straps to secure the tank in place.

## Software
For software, we currently only support building from source. The verm-wasp-drone repository contains a link to a submodule called rjc. In the rjc repository, the README contains instructions on how to build from source.

### RJCamera (rjc)
Build rjc from source with the following commands:
```
    bash configure.sh
    qmake6
    make
    ./rjc
```

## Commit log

2025-04-30 CAD stl files
    [Here3 straddle mount.stl, S550 CubeOrange vibration mount - BOTTOM.stl, S550 CubeOrange vibration mount - TOP.stl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]
2025-04-30 update cad files
    [Here3 straddle mount.stl, S550 CubeOrange vibration mount - BOTTOM.stl, S550 CubeOrange vibration mount - TOP.stl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]
